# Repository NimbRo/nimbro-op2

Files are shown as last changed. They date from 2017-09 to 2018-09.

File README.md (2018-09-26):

NimbRo-OP2 and NimbRo-OP2X hardware release
===========================

This repository contains all hardware aspects of the NimbRo-OP2 and NimbRo-OP2X robots split into separate folders.

NimbRo-OP2             |  NimbRo-OP2X
:-------------------------:|:-------------------------:
  |  
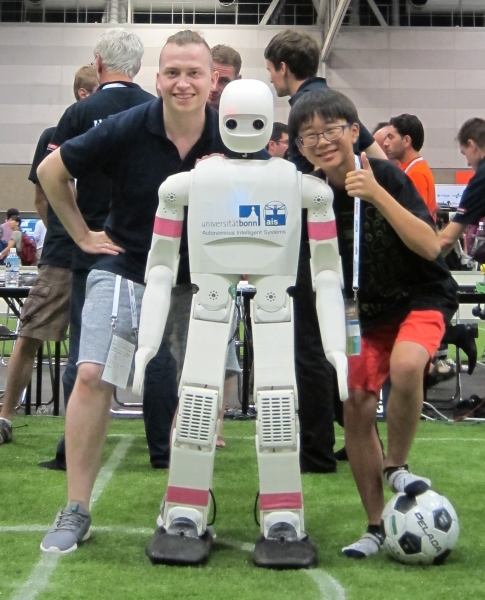
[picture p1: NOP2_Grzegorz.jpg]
NimbRo-OP2
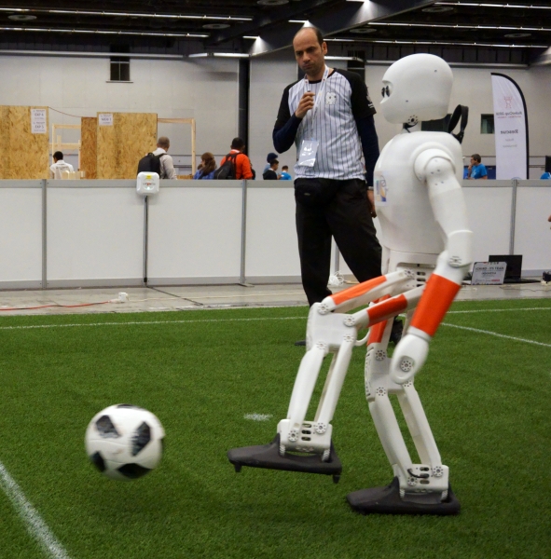
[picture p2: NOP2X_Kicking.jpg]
NimbRo-OP2 NimbRo-OP2X
 | 

A bill of materials (bom) file containing part numbers and quantities is included in each directory related to the robot.
Part files in *.STEP format have been put in the CAD folder. 
These include:
* 3D printable parts
* Milled brass gears (NimbRo-OP2 only)
* 3D printable gears (alternative for NimbRo-OP2 and default for NimbRo-OP2X)

Authors & License
-----------------

The NimbRo-OP2(X) robots have been developed at the [Autonomous Intelligent Systems Group](http://ais.uni-bonn.de),
[Rheinische Friedrich-Wilhelms-Universität Bonn](http://www.uni-bonn.de). 
The CAD drawings in this repository are released under the Attribution-NonCommercial-ShareAlike 3.0 (CC BY-NC-SA 3.0) license 
(see "HARDWARE LICENSE CreativeCommonsLicense CC BY-NC-SA 3.0.txt" for details).

Reference & Citation
--------------------

To reference and/or cite the work contained in this repository, please use the following publications:

Grzegorz Ficht, Philipp Allgeuer, Hafez Farazi, and Sven Behnke:
NimbRo-OP2: Grown-up 3D Printed Open Humanoid Platform for Research
In Proceedings of IEEE-RAS International Conference on Humanoid Robots (Humanoids), Birmingham, UK, November 2017.

Grzegorz Ficht, Hafez Farazi, Andre Brandenburger, Diego Rodriguez, Dmytro Pavlichenko, Philipp Allgeuer, Mojtaba Hosseini, and Sven Behnke:
NimbRo-OP2X: Adult-sized Open-source 3D Printed Humanoid Robot
Accepted for IEEE-RAS 18th International Conference on Humanoid Robots (Humanoids), Beijing, China, to appear November 2018. 

Video
-----

To see the NimbRo-OP2 in action, please see the video at:
http://www.ais.uni-bonn.de/videos/Humanoids_2017/
A video displaying the NimbRo-OP2X can be seen here:
https://www.youtube.com/watch?v=qmYSt3nVJpA

Links
-----

For more information, take a look at our webpages:

* NimbRo-OP2: http://nimbro.net/OP
* Autonomous Intelligent Systems: http://ais.uni-bonn.de

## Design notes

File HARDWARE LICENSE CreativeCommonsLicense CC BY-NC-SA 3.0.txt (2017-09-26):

This is a human-readable summary of the Legal Code (the full licence).
The full license can be optained here:
http://creativecommons.org/licenses/by-nc-sa/3.0/legalcode 

All data in this Repository is published under the following License

Attribution-NonCommercial-ShareAlike 3.0 CC BY-NC-SA 3.0 

This means:

You are free:
* to copy, distribute, display, and perform the work. 
* to make derivative works.

Under the following conditions:
Attribution — You must give the original author credit.
Non-Commercial — You may not use this work for commercial purposes. 
Share Alike — If you alter, transform, or build upon this work, you may distribute the resulting work only under a licence identical to this one.

With the understanding that:
Waiver — Any of the above conditions can be waived if you get permission from the copyright holder.
Public Domain — Where the work or any of its elements is in the public domain under applicable law, that status is in no way affected by the license.
Other Rights — In no way are any of the following rights affected by the license:
* Your fair dealing or fair use rights, or other applicable copyright exceptions and limitations;
* The author's moral rights;
* Rights other persons may have either in the work itself or in how the work is used, such as publicity or privacy rights.
Notice — For any reuse or distribution, you must make clear to others the licence terms of this work.

Rheinische Friedrich-Wilhelms-Universität Bonn
Institut für Informatik VI
Friedrich-Ebert-Allee 144
53113 Bonn 
Germany
www.ais.uni-bonn.de

Thanks to creativecommons.org !!!

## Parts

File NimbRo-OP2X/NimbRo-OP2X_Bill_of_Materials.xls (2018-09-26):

Nr | Item name | MPN | Manufacturer | Qty | Comment
 | Structural Components
1 | 3D printed part | Gear16T |  | 8 | recommended durable gear printing service: http://www.igus.eu/wpck/18788/N17_08_02_SLS_Material
2 | 3D printed part | Gear21T |  | 1 | recommended durable gear printing service: http://www.igus.eu/wpck/18788/N17_08_02_SLS_Material
3 | 3D printed part | Gear30T |  | 1 | recommended durable gear printing service: http://www.igus.eu/wpck/18788/N17_08_02_SLS_Material
4 | 3D printed part | Gear40T |  | 1 | recommended durable gear printing service: http://www.igus.eu/wpck/18788/N17_08_02_SLS_Material
5 | 3D printed part | HeadFaceMask |  | 1
6 | 3D printed part | HeadLeftSideCover |  | 2
7 | 3D printed part | HeadMainPart |  | 1
8 | 3D printed part | HeadRightSideCover |  | 1
9 | 3D printed part | KneeFanHolder |  | 2
10 | 3D printed part | LeftArmUpperMainPart |  | 2 | Should be glued in under left/right foot
11 | 3D printed part | LeftFoot |  | 2
12 | 3D printed part | LeftRightAnkleHipCage |  | 2
13 | 3D printed part | LeftRightAnkleHipGearCover |  | 2
14 | 3D printed part | LeftRightArmLowerMainPart |  | 2
15 | 3D printed part | LeftRightFootLid |  | 4
16 | 3D printed part | LeftRightHip |  | 4
17 | 3D printed part | LeftRightKneeCage |  | 4
18 | 3D printed part | LeftRightKneeSide |  | 1
19 | 3D printed part | LeftRightLowerUpperArmCover |  | 2
20 | 3D printed part | LeftRightThighShankBack |  | 1
21 | 3D printed part | LeftRightThighShankFront |  | 1
22 | 3D printed part | LeftShoulder |  | 1
23 | 3D printed part | NeckPart |  | 1
24 | 3D printed part | RightArmUpperMainPart |  | 2
25 | 3D printed part | RightFoot |  | 1
26 | 3D printed part | RightShoulder |  | 1
27 | 3D printed part | Trunk |  | 1
28 | 4D printed part | TrunkBatteryHolder |  | 8
29 | 4D printed part | TrunkCoverBottom |  | 8
30 | 5D printed part | TrunkCoverMain |  | 2
31 | 5D printed part | TrunkCoverTop |  | 2
32 | 6D printed part | TrunkMiniITXholder |  | 8
33 | Dry rubbing bearing 20mm inner dia., 30mm outer dia., 2mm thick |  | igus | 2 | used for shoulder pitch, inside diameter needs to be slightly shaved off
34 | igus PRT slewing ring bearing – type 02 | PRT-02-20-AL | igus | 2 | S2 hole diameter needs to be drilled to 5,0-5,1mm
 | Electronics
35 | XM540-W270(R/T) Dynamixel actuator | R: 902-0133-000 | Robotis | 34 | 13 per leg, 3 per arm, 2 in head
36 | Set of Cables X4P | R: 903-0244-000 (180mm) R: 903-0245-000 (240mm) | Robotis | 1 | depending on the purchased servos, a 3-lead wire (T) or 4-lead wire (R) set is needed
37 | Master Slave Sync Cables | 903-0232-000 | Robotis | 16 | The bare minimum of cables is 12, but having spares is good, as they tend to break
38 | CM740 Controller with cable set and buttons |  | Robotis | 1 | http://support.robotis.com/en/product/robotis-op2/sub_controller(cm-740).htm
39 | Power Switch from DW-EK02 set | 903-0202-000 | Robotis | 1 | part of ROBOTIS-OP set
40 | Logitech C905 HD Camera |  | Logitech | 1 | optionally two, for stereo image
41 | Wide angle lens IRC 2/3Inch M12x0.5, 2.0mm, 1:2.0 195°, image circle diameter 6.54 |  | Lensation | 2 | only one is needed for actual usage, for visual appearance and/or stereo-vision 2 are recommended
42 | Reflective IR-cut filter, diameter 9.5mm, thickness 0.3mm T50@650nm | Lensagon BF2M2020S23 | Lensation | 1 | The lens should be purchased with the filter already glued to it.
43 | Lens mount M12 20mm | IRC650-D95T03 | StockOptics | 1 | http://www.stockoptics.com/board-lens-holder.html ; optionally two, for stereo image
44 | 4S 14.8V LiPo Battery 8000mAh |  | ZIPPY | 1 | https://hobbyking.com/en_us/zippy-flightmax-8000mah-4s1p-30c.html
 | Rest of mechanics |  |  |  | for all screws, we recommend imbus heads - values and types will be verified still
45 | M2.5x6 screw
46 | M2.5x8 screw
47 | M3x8 screw
48 | M3 square nut
49 | M2.5 regular nut
50 | Threadlocking adhesive 200 series |  | LOCTITE |  | 50ml bottle
51 | M5 Rubber cleats |  |  | 8 | optional (for feet)
52 | M5 Nuts |  |  | 8 | optional (for feet)
53 | M5 square nuts |  |  | 12 | Press fits into torso to mount hip yaw axis
54 | M5x40 countersunk screw |  |  | 12 | mounting of hip axis to torso
55 | M5x16 screw |  |  | 12 | connects rotating hip part to PRT bearing
56 | F623ZZ bearing |  |  | 28 | Bearing that goes into free-wheeling horn
 | Computer |  |  |  | PC configuration put in for reference
57 | Mainboard | Z370M-ITX/ac | ASRock | 1
58 | Processor | i7-8700T | Intel | 1 | the "T" version is important - it's the low current version
59 | GPU | GeForce GTX 1050 Ti | MSI | 1 | Low profile version necessary. Although the GPU altogether is optional, for deep learning capabitilities.
60 | CPU Cooler | CNPS2X | Zalman | 1 | Very light-weight cooler
61 | Power Supply | M4-ATX | Mini-Box | 1 | power supply for the PC
62 | SSD hard drive (M.2 slot) |  |  | 1
63 | DDR4 RAM |  |  | 1 | 4/8 GB minimum
 | General comments:
 | Screw quantities are overestimated by 100pcs so the user always has some spares and in cases where user modifications may take place
 | The user will of course need a set of tools and some other materials to build the robot (e.g. electrical tape, hot glue, zip ties, allen keys, etc.)

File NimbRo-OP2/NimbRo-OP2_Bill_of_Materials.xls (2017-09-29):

Nr | Item name | MPN | Manufacturer | Qty | Comment
1 | 3D printed part | GearCover |  | 8
2 | 3D printed part | HeadFaceMask |  | 1
3 | 3D printed part | HeadLeftSideCover |  | 1
4 | 3D printed part | HeadMainPart |  | 1
5 | 3D printed part | HeadRightSideCover |  | 1
6 | 3D printed part | LeftAnkleHip |  | 2
7 | 3D printed part | LeftArmUpperMainPart |  | 1
8 | 3D printed part | LeftFoot |  | 1
9 | 3D printed part | LeftRightArmUpperMainPart |  | 2
10 | 3D printed part | LeftRightFootLid |  | 2 | Should be glued in under left/right foot
11 | 3D printed part | LeftRightHip |  | 2
12 | 3D printed part | LeftRightKneeBackCover |  | 2
13 | 3D printed part | LeftRightKneeFrontCover |  | 2
14 | 3D printed part | LeftRightKneeMainPart |  | 2
15 | 3D printed part | LeftRightLegThighShankBack |  | 4
16 | 3D printed part | LeftRightLegThighShankFront |  | 4
17 | 3D printed part | LeftRightLowerUpperArmCover |  | 4
18 | 3D printed part | LeftShoulder |  | 1
19 | 3D printed part | RightAnkleHip |  | 2
20 | 3D printed part | RightArmUpperMainPart |  | 1
21 | 3D printed part | RightFoot |  | 1
22 | 3D printed part | RightShoulder |  | 1
23 | 3D printed part | Trunk |  | 1
24 | 3D printed part | TrunkBackCoverInsert |  | 2
25 | 3D printed part | TrunkBackCoverMain |  | 1
26 | 3D printed part | TrunkBatteryHolder |  | 1
27 | 3D printed part | TrunkPCHolder |  | 1
28 | M1 35T brass gear | Gear1035machined |  | 8 | 26303500 Used as raw material, alternatively use 3D printed version below (http://www.maedler.de/Article/26303500)
29 | M1 70T brass gear | Gear1070machined |  | 8 | 26307000 Used as raw material, alternatively use 3D printed version below (http://www.maedler.de/Article/26307000)
30 | M1 48T brass gear | Gear1048machined |  | 2 | 26304800 Used as raw material, alternatively use 3D printed version below (http://www.maedler.de/Article/26304800)
31 | M1 96T brass gear | Gear1096machined |  | 2 | 26309600 Used as raw material, alternatively use 3D printed version below (http://www.maedler.de/Article/26309600)
32 | M1 35T SLS printed gear | Gear1035printed |  | 8 | recommended durable gear printing service: http://www.igus.eu/wpck/18788/N17_08_02_SLS_Material
33 | M1 70T SLS printed gear | Gear1070printed |  | 8 | recommended durable gear printing service: http://www.igus.eu/wpck/18788/N17_08_02_SLS_Material
34 | M1 48T SLS printed gear | Gear1048printed |  | 2 | recommended durable gear printing service: http://www.igus.eu/wpck/18788/N17_08_02_SLS_Material
35 | M1 96T SLS printed gear | Gear1096printed |  | 2 | recommended durable gear printing service: http://www.igus.eu/wpck/18788/N17_08_02_SLS_Material
36 | Milled aluminium neck part | NeckPartMilled |  | 1 | used to connect the head pitch to neck yaw
37 | 3D Printed neck part | NeckPartPrinted |  | 1 | used as an alternative to the above
38 | Dry rubbing bearing 20mm inner dia., 30mm outer dia., 2mm thick |  | igus | 2 | used for shoulder pitch, inside diameter needs to be slightly shaved off
39 | igus PRT slewing ring bearing – type 02 | PRT-02-30-AL | igus | 2 | S2 hole diameter needs to be drilled to 5,0-5,1mm
40 | MX106(R/T) Dynamixel actuator | R: 902-0070-000 T: 902-0060-000 | Robotis | 34 | 13 per leg, 3 per arm, 2 in head
41 | Set of Cables |  | Robotis | 1 | depending on the purchased servos, a 3-lead wire (T) or 4-lead wire (R) set is needed
42 | CM730 / CM740 Controller with cable set and buttons | R: 902-0072-000 T: 902-0061-000 | Robotis | 1 | CM730 is discontinued, although still supported
43 | HN05-I101 Idler bearing set | 902-0057-000 | Robotis | 29 | head yaw, hip yaw and shoulder pitch don't use idler bearings
44 | HN05-N102 Servo horn set | 903-0157-000 | Robotis | 34
45 | Power Switch from DW-EK02 set | 903-0202-000 | Robotis | 1 | part of ROBOTIS-OP set
46 | Power cable for PC from DW-EK02 set |  | Robotis | 1 | cable supplies power from CM740 to PC, needs to be soldered on the PC or modified to use the proper connector on the PC side
47 | Logitech C905 HD Camera |  | Logitech | 1 | optionally two, for stereo image
48 | Wide angle lens IRC 2/3Inch M12x0.5, 2.0mm, 1:2.0 195°, image circle diameter 6.54 |  | Lensation | 2 | only one is needed for actual usage, for visual appearance and/or stereo-vision 2 are recommended
49 | Reflective IR-cut filter, diameter 9.5mm, thickness 0.3mm T50@650nm | Lensagon BF2M2020S23 | Lensation | 1 | optionally two, for stereo image
50 | Lens mount M12 20mm | IRC650-D95T03 | StockOptics | 1 | http://www.stockoptics.com/board-lens-holder.html ; optionally two, for stereo image
51 | M2.5x4 screw |  |  | 4 | used in neck yaw horn exclusively – these screws are included with the servo horn set, no need to buy them
52 | M2.5x6 screw |  |  | 700 | Used in rest of horns and idle bearing connections, except from receiving gear in hip/ankle roll
53 | M2.5x8 screw |  |  | 700 | used in mounting servos to plastic, in ankle/hip roll, M2.5x8 would suffice in many places, but due to tolerances M2.5x10 seems to be a better option
54 | M3x8 screw |  |  | 100 | used for screwing shell parts together (eye mask, head/arm/knee/gear covers and so on)
55 | M3 square nut |  |  | 100 | need to be glued into prepared holes (eye mask, head/arm/knee/gear covers and so on)
56 | M2.5 regular nut |  |  | 600 | press fitted into servos to allow mounting inside case
57 | Threadlocking adhesive 200 series |  | LOCTITE | 1 | 50ml bottle
58 | M5 Rubber cleats |  |  | 8 | optional
59 | M5 Nuts |  |  | 8 | optional
60 | M5 square nuts |  |  | 16 | Press fits into torso to mount hip yaw axis
61 | M5x30 countersunk screw |  |  | 16 | mounting of hip axis to torso
62 | M5x16 screw |  |  | 8 | connects rotating hip part to PRT bearing
63 | Computing unit | NUC7I7BNH | Intel | 1 | model of PC put in for reference, any compact PC should be able to fit, after printing a suitable support plate and port cover; RAM and SSD not included
64 | 4S 14.8V LiPo Battery 8000mAh |  | ZIPPY | 1 | https://hobbyking.com/en_us/zippy-flightmax-8000mah-4s1p-30c.html
 | General comments:
 | Screw quantities are overestimated by 100pcs so the user always has some spares and in cases where user modifications may take place
 | The user will of course need a set of tools and some other materials to build the robot (e.g. electrical tape, hot glue, zip ties, allen keys, etc.)

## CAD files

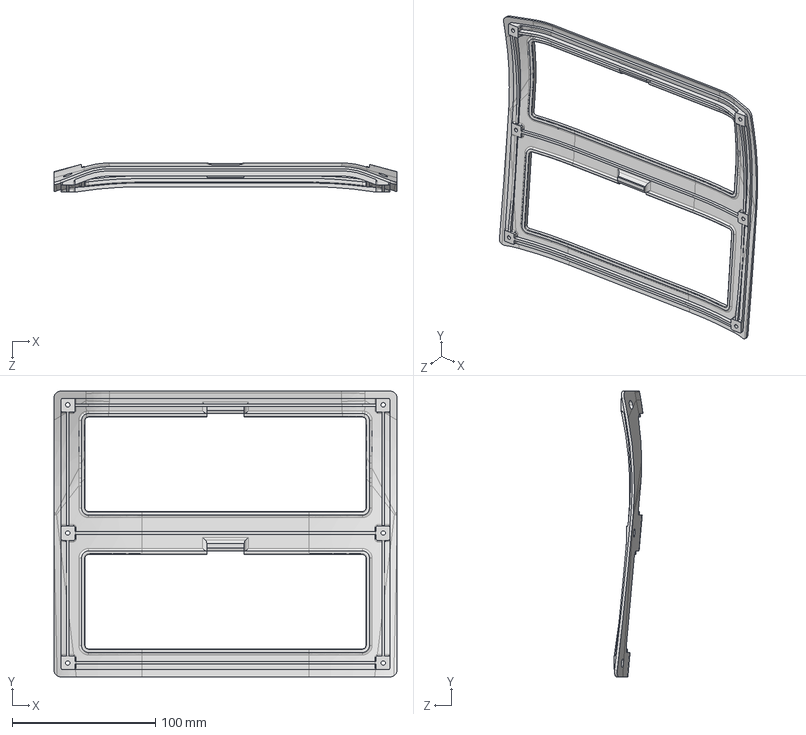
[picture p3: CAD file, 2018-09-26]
NimbRo-OP2X/CAD/TrunkCoverMain.STEP
239.2 x 199.2 x 20.3 mm

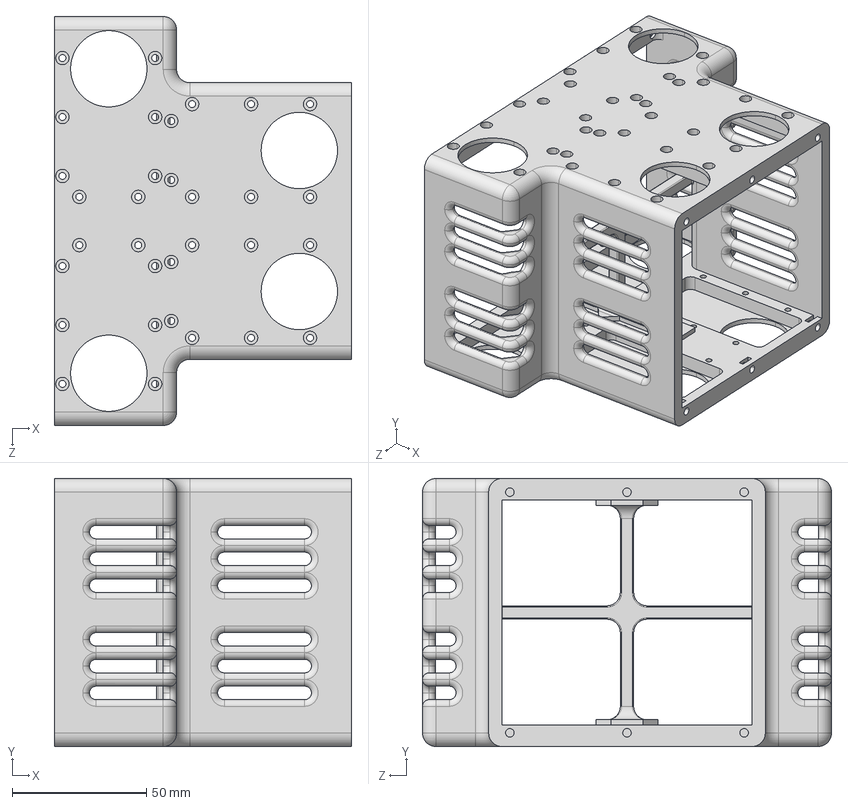
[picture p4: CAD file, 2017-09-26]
NimbRo-OP2/CAD/LeftRightKneeMainPart.STEP
110.9 x 100.0 x 152.6 mm

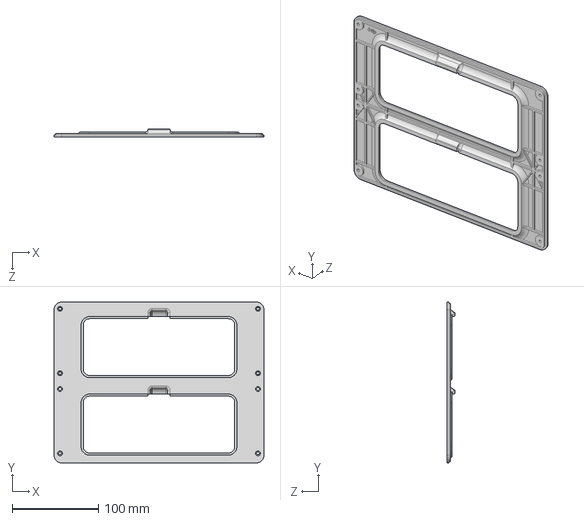
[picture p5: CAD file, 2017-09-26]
NimbRo-OP2/CAD/TrunkBackCoverMain.STEP
244.0 x 187.0 x 8.95 mm

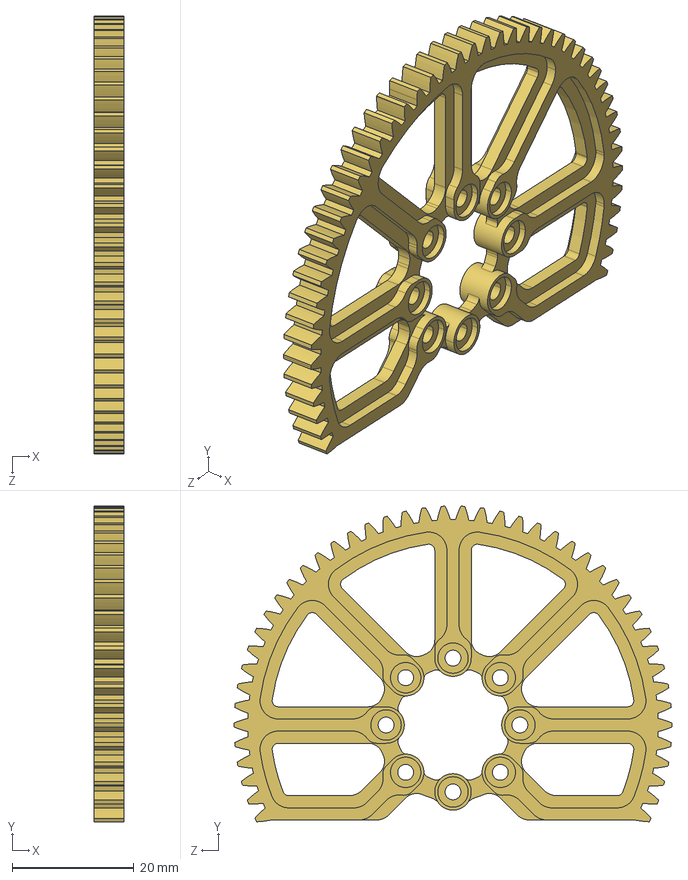
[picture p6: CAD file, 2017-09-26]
NimbRo-OP2/CAD/Gear1070machined.STEP
5.00 x 51.9 x 72.0 mm

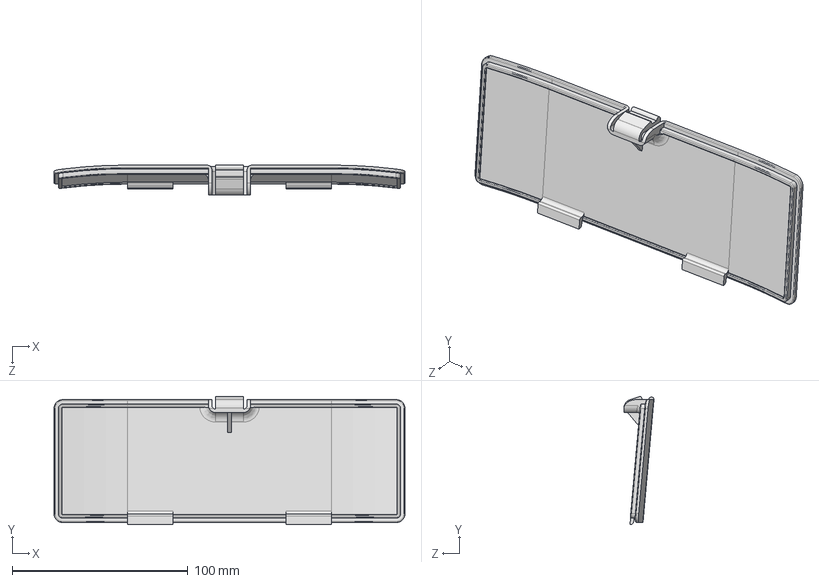
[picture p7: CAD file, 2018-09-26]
NimbRo-OP2X/CAD/TrunkCoverBottom.STEP
200.0 x 73.0 x 17.2 mm

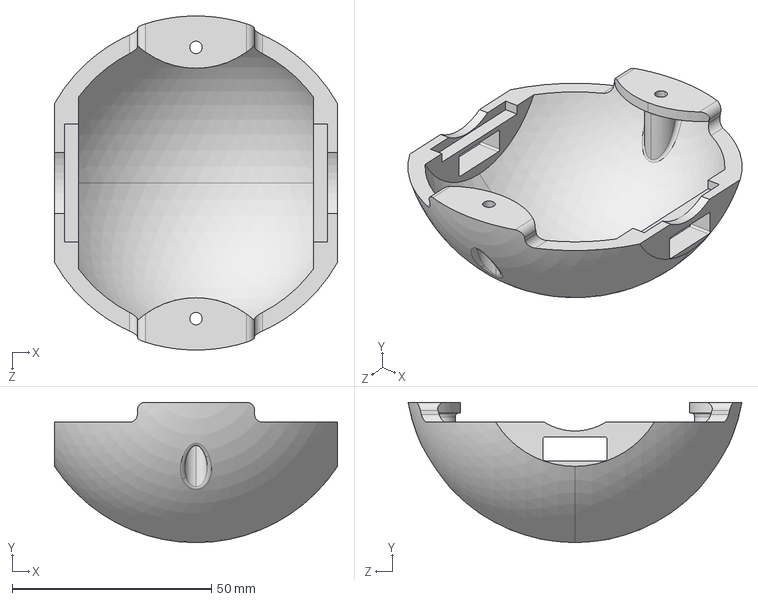
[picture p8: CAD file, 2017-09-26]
NimbRo-OP2/CAD/LeftRightLowerUpperArmCover.STEP
71.0 x 35.2 x 83.7 mm

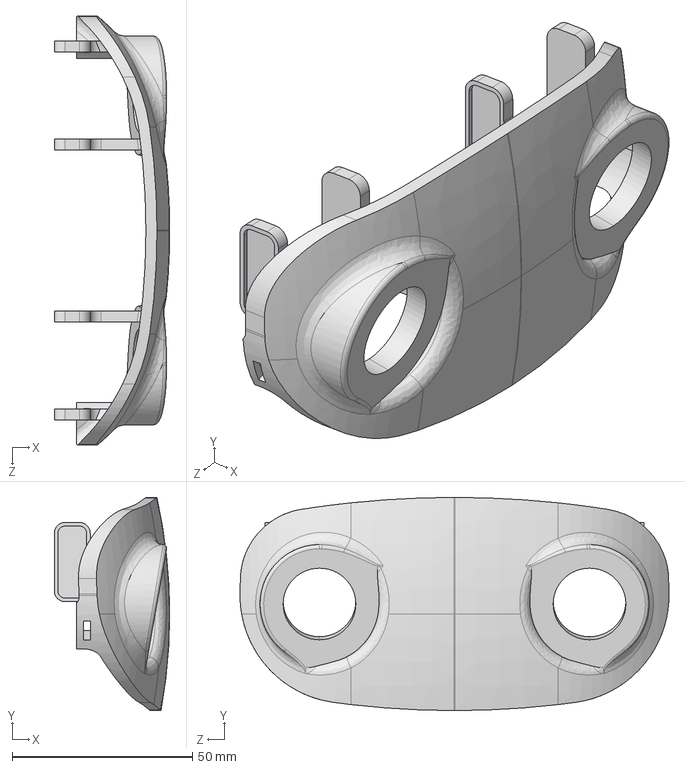
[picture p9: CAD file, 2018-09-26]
NimbRo-OP2X/CAD/HeadFaceMask.STEP
32.1 x 59.2 x 119.1 mm

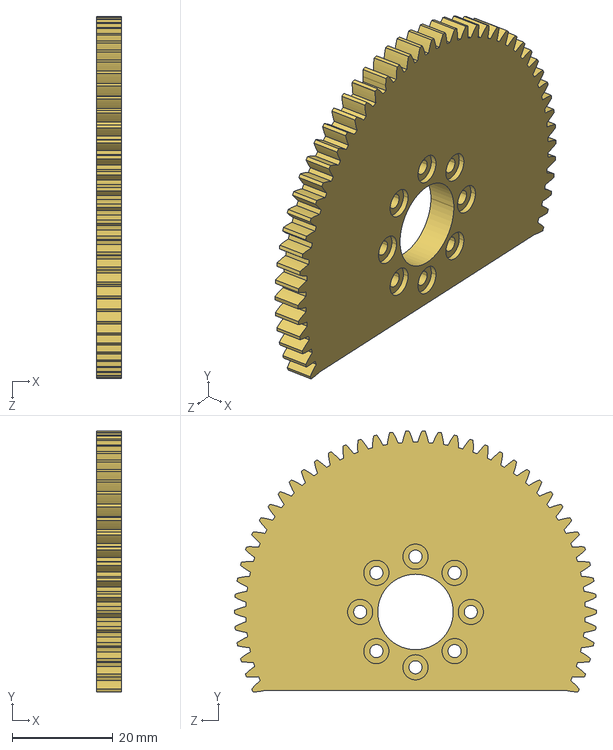
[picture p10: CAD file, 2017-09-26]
NimbRo-OP2/CAD/Gear1070printed.STEP
5.00 x 51.9 x 72.0 mm

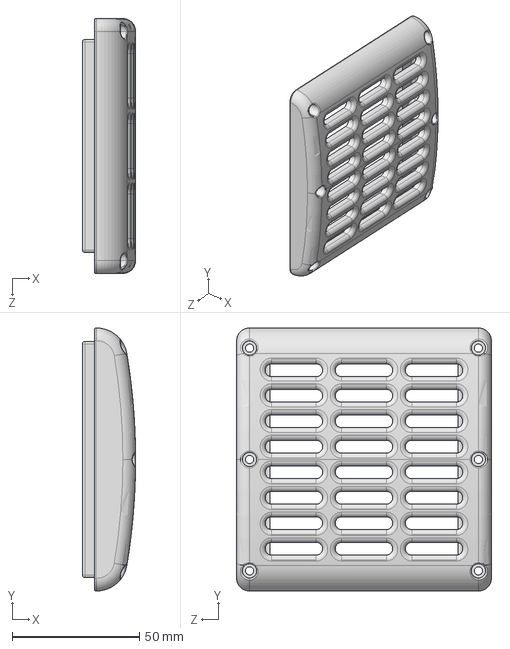
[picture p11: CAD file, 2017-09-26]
NimbRo-OP2/CAD/LeftRightKneeBackCover.STEP
20.9 x 103.2 x 100.0 mm

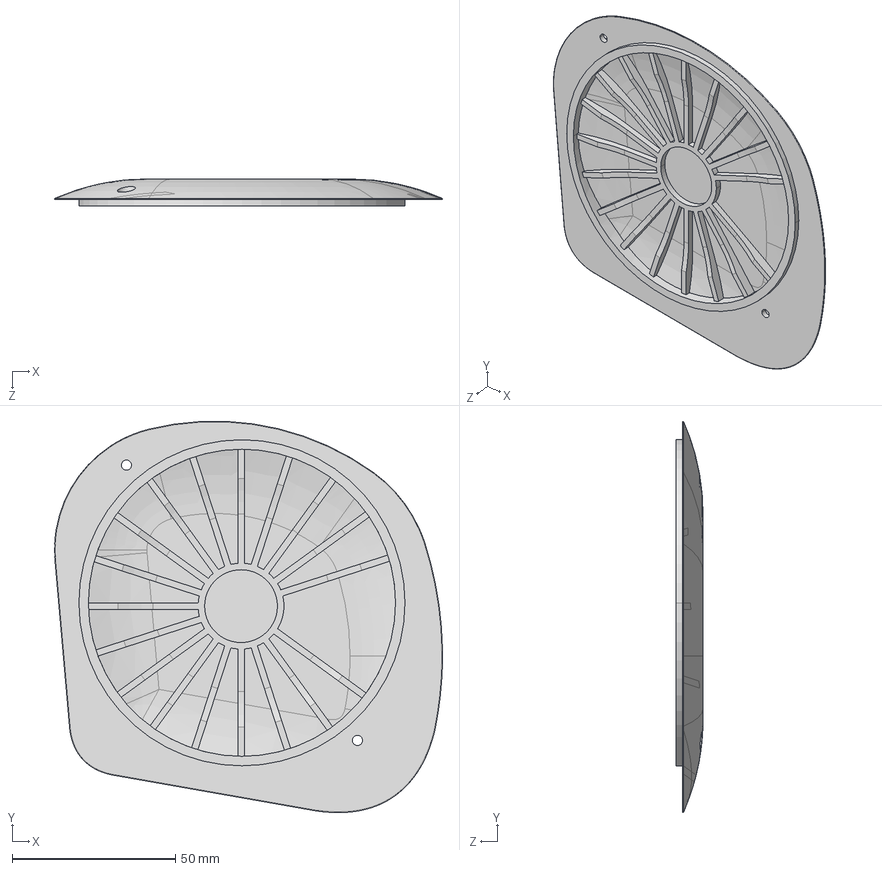
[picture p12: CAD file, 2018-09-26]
NimbRo-OP2X/CAD/HeadLeftSideCover.STEP
118.8 x 119.7 x 8.30 mm

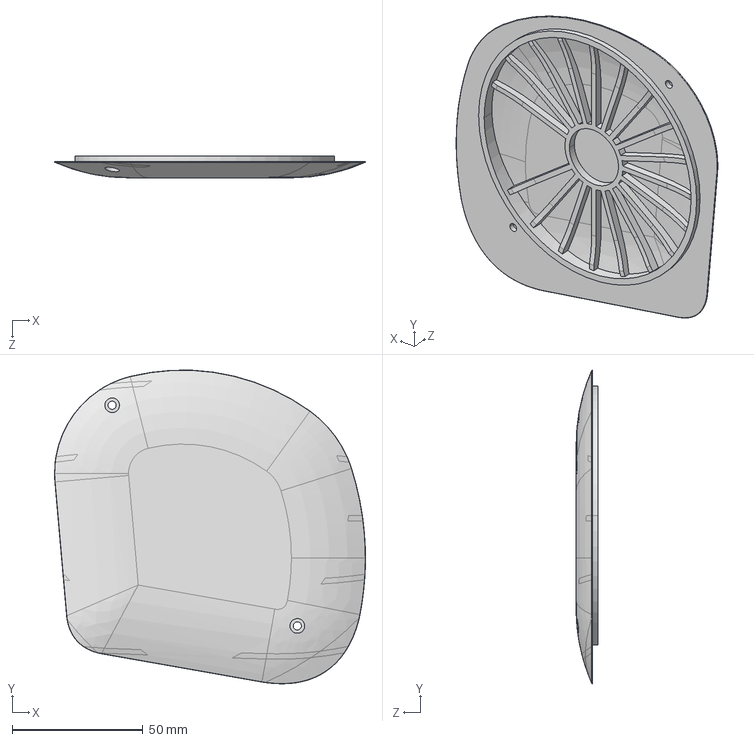
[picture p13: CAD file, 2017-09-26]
NimbRo-OP2/CAD/HeadRightSideCover.STEP
118.8 x 119.7 x 8.30 mm

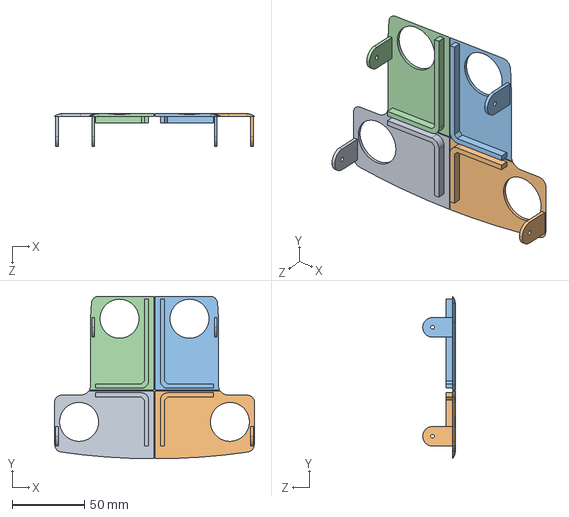
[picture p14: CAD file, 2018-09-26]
NimbRo-OP2X/CAD/LeftRightKneeSide.STEP
138.6 x 112.6 x 22.6 mm

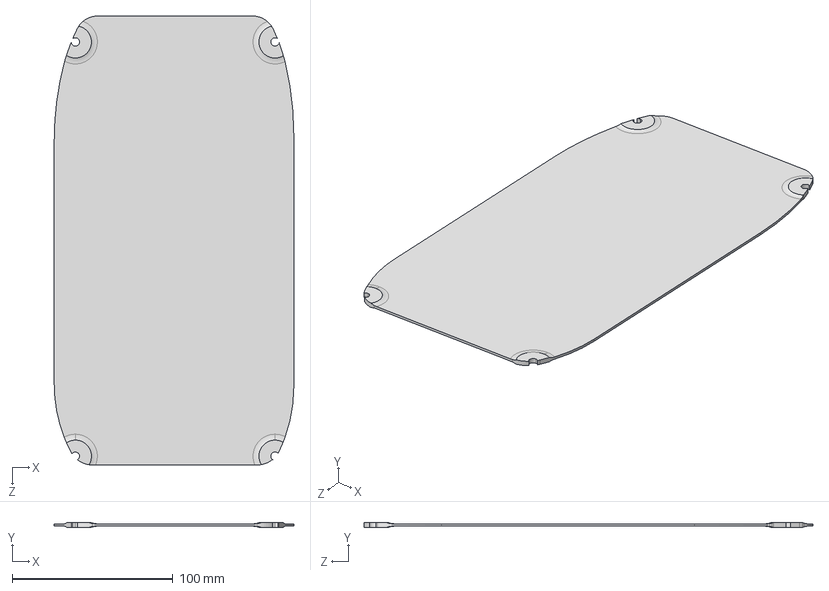
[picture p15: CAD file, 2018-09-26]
NimbRo-OP2X/CAD/LeftRightFootLid.STEP
148.8 x 2.90 x 278.9 mm

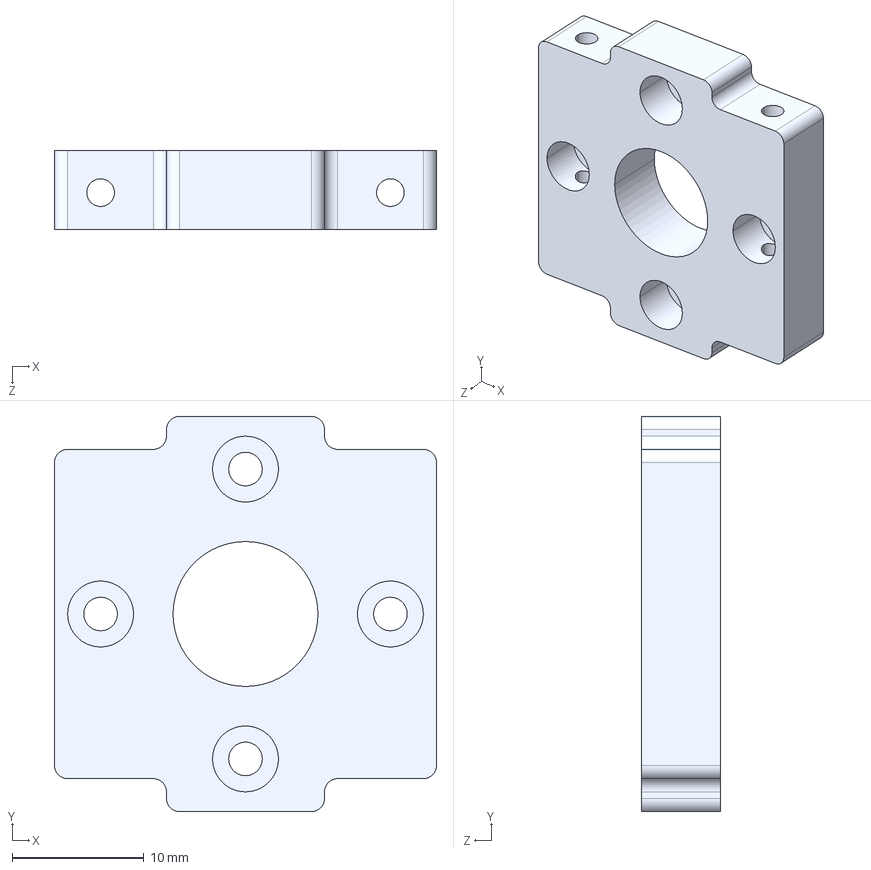
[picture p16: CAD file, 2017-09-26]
NimbRo-OP2/CAD/NeckPartMilled.STEP
29.0 x 30.0 x 6.00 mm

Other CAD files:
NimbRo-OP2X/CAD/KneeFanHolder.STEP
NimbRo-OP2/CAD/NeckPartPrinted.STEP
NimbRo-OP2X/CAD/LeftRightAnkleHipGearCover.STEP
NimbRo-OP2/CAD/TrunkPCHolder.STEP
NimbRo-OP2/CAD/Gear1035machined.STEP
NimbRo-OP2/CAD/Gear1035printed.STEP
NimbRo-OP2/CAD/Gear1048machined.STEP
NimbRo-OP2/CAD/Gear1048printed.STEP
NimbRo-OP2/CAD/Gear1096machined.STEP
NimbRo-OP2/CAD/Gear1096printed.STEP
NimbRo-OP2/CAD/GearCover.STEP
NimbRo-OP2/CAD/HeadFaceMask.STEP
NimbRo-OP2/CAD/HeadLeftSideCover.STEP
NimbRo-OP2/CAD/LeftAnkleHip.STEP
NimbRo-OP2/CAD/LeftRightFootLid.STEP
NimbRo-OP2/CAD/LeftRightKneeFrontCover.STEP
NimbRo-OP2/CAD/LeftRightLegThighShankBack.STEP
NimbRo-OP2/CAD/LeftRightLegThighShankFront.STEP
NimbRo-OP2/CAD/RightAnkleHip.STEP
NimbRo-OP2/CAD/TrunkBackCoverInsert.STEP
NimbRo-OP2/CAD/TrunkBatteryHolder.STEP
NimbRo-OP2X/CAD/HeadRightSideCover.STEP
NimbRo-OP2X/CAD/LeftRightLowerUpperArmCover.STEP
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

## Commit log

2017-09-26 Hardware Release - NimbRo-OP2
    [Gear1035machined.STEP, Gear1035printed.STEP, Gear1048machined.STEP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]
2017-09-29 updated readme, added picture
    [NimbRo-OP2_Bill_of_Materials.xls]
2018-09-26 reorganised structure
    [Gear1035machined.STEP, Gear1035printed.STEP, Gear1048machined.STEP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]
2018-09-26 added OP2X hardware
    [HeadFaceMask.STEP, HeadLeftSideCover.STEP, HeadRightSideCover.STEP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]
